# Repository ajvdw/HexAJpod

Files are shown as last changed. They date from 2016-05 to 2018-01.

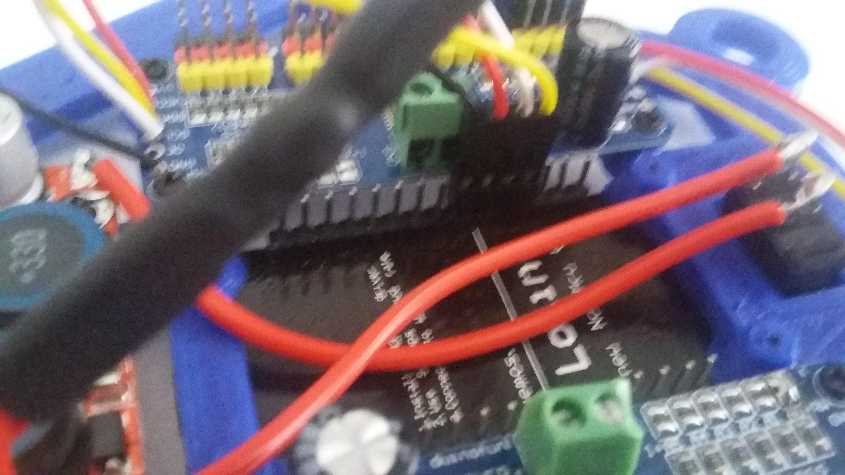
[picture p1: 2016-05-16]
media/nodemcu.jpg

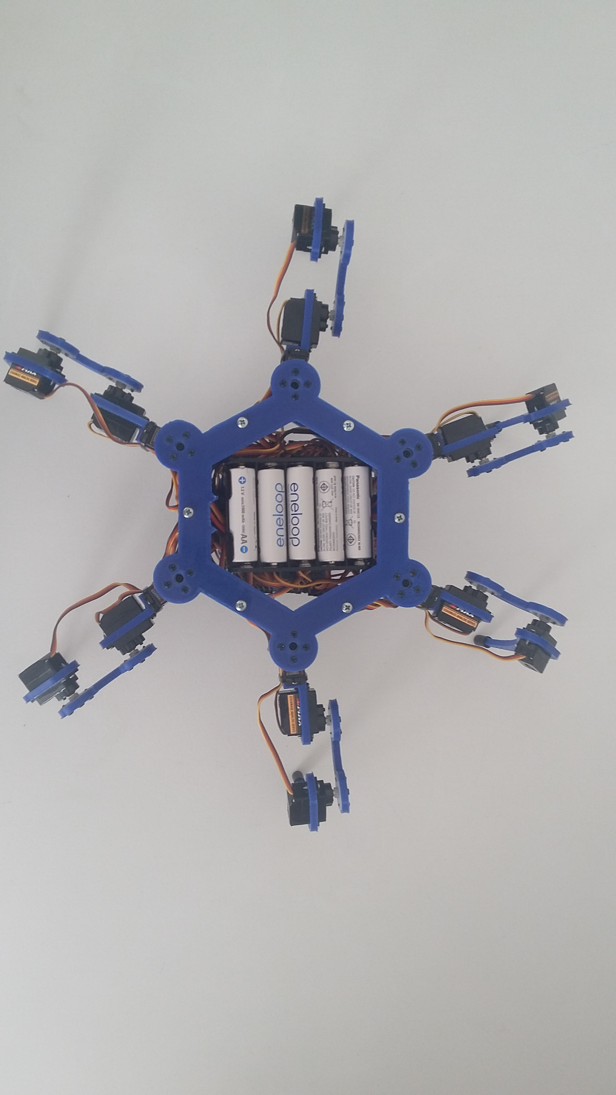
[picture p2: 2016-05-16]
media/top.jpg

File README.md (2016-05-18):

# HexAJpod
Hexapod ESP8266

This repository contains

- OpenScad cad design file for a 3d printed hexapod
- stl files for printing
- hexapod firmware for the ESP8266 Arduino IDE

Have a look at: https://youtu.be/j8itndjbUWE

The hexapod will act as an Wifi Access point.
You can connect to it using the password (bestkeptsecret).
Open a web page and visit http://192.168.4.1 
This opens a page with the remote control.
When fully loaded, a websocket connection is opened.

You should be able to build it for less than 100$

Bill of Materials:

1 NodeMCU - an ESP8266 development board by LoLin (v3)

2 Led / Servo drivers based on PCA9685

18 Servos by EMAX - ES08MA II, these have metal gears

5 NiMh AA Eneloop Batteries by Panasonic 

1 Battery holder for 5 AA batteries

1 DC-DC converter to converter to get a clean 3.3V

18 M3 screws 12mm

6 End caps (5mm)

6 Bearings 623Z (id=3mm, od=10mm)

6 M3 washers

6 M3 nuts

6 Brass 40mm Standoffs (M3 threaded)

75 2mm x 6mm screws

25 2mm x 8mm screws

I ordered the parts on eBay (http://r.ebay.com/3nL8qE)

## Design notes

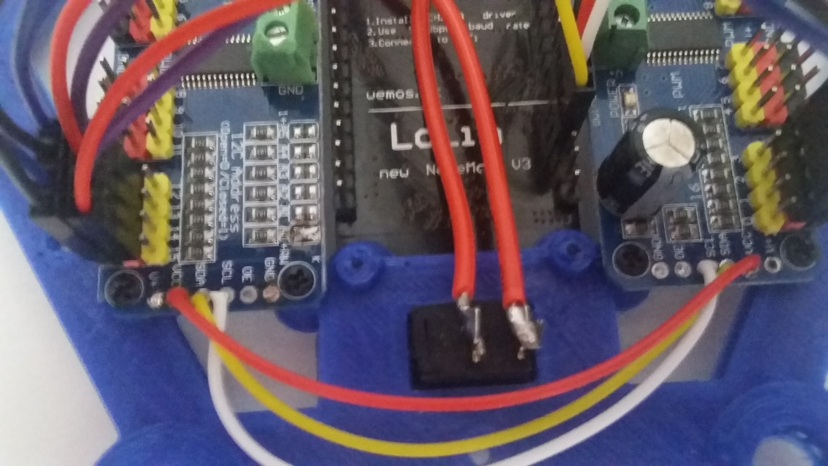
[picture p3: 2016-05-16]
media/switch.jpg

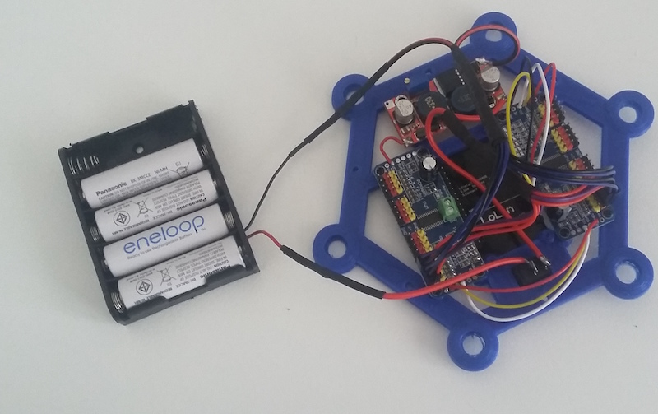
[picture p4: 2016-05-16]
media/thumbnail.jpg

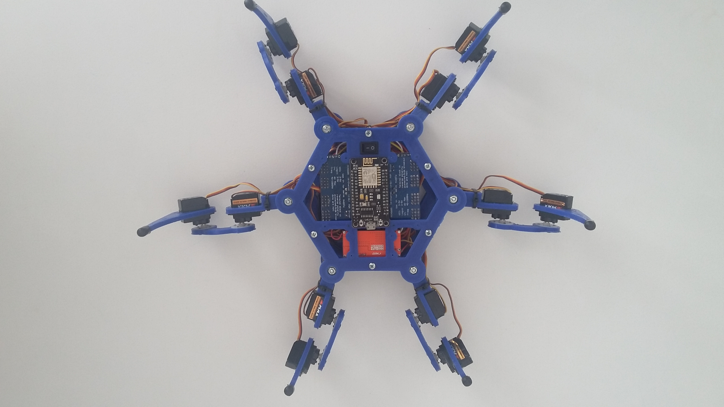
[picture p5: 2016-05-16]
media/bottom.jpg

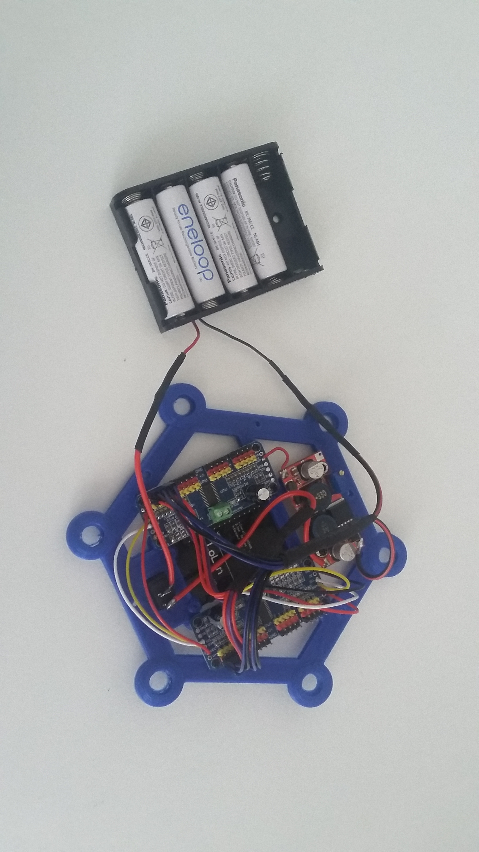
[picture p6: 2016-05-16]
media/internal.jpg

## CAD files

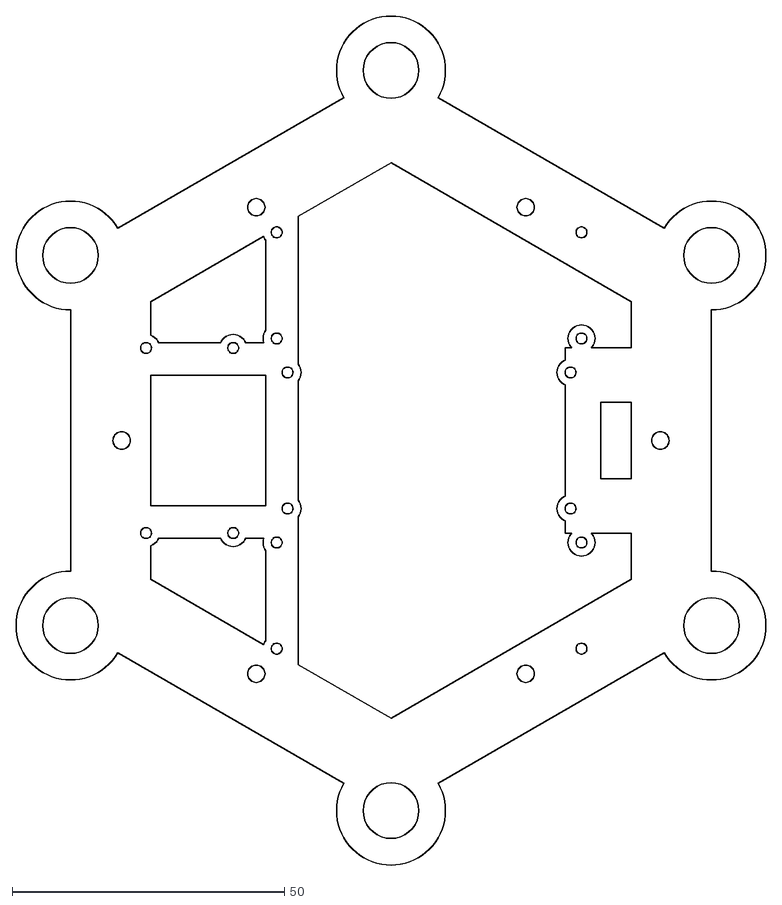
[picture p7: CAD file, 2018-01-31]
openscad/hexajpodbottom.dxf
137.8 x 156.0

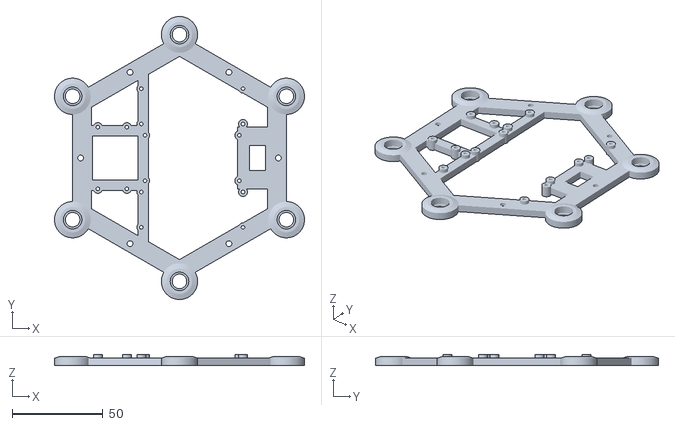
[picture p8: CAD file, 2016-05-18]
stl/bottom.stl
137.8 x 156.0 x 6.00

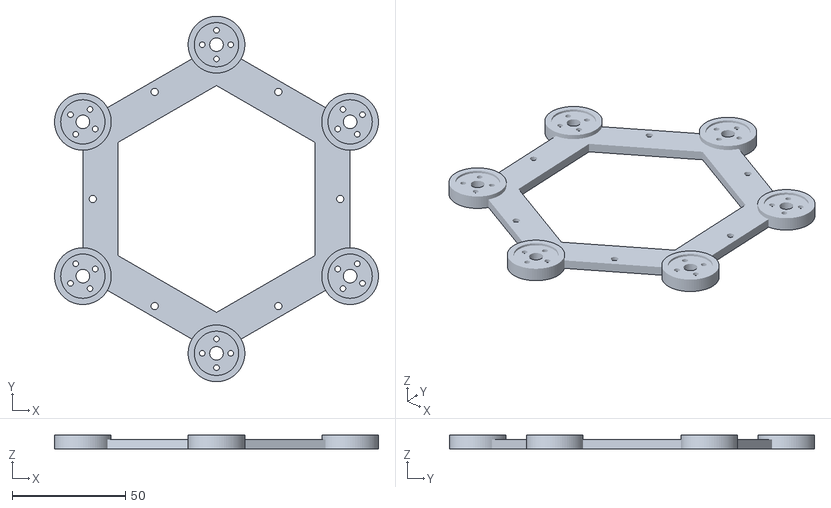
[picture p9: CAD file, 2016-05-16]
stl/top.stl
142.8 x 161.0 x 6.00

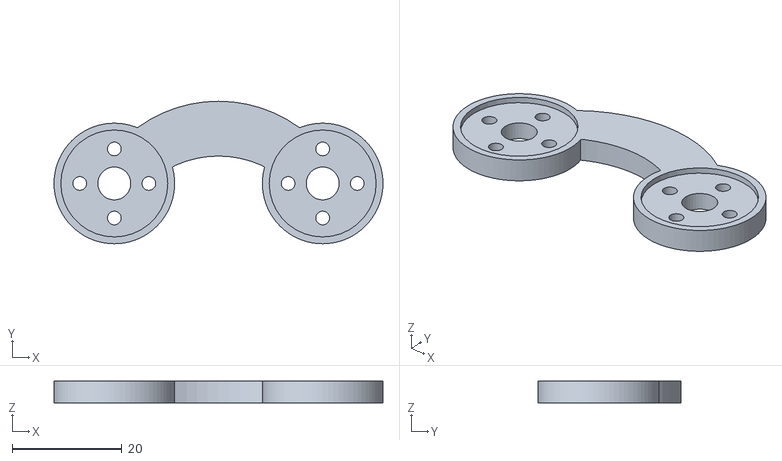
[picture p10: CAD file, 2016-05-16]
stl/femur.stl
60.0 x 26.0 x 4.00

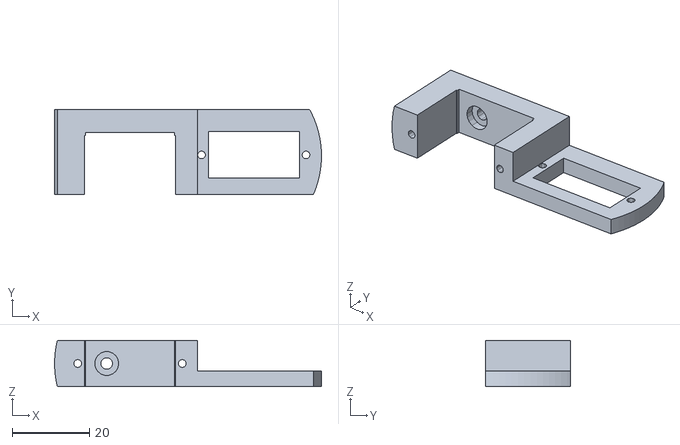
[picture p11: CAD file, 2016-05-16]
stl/coxa_l.stl
69.0 x 22.0 x 12.0

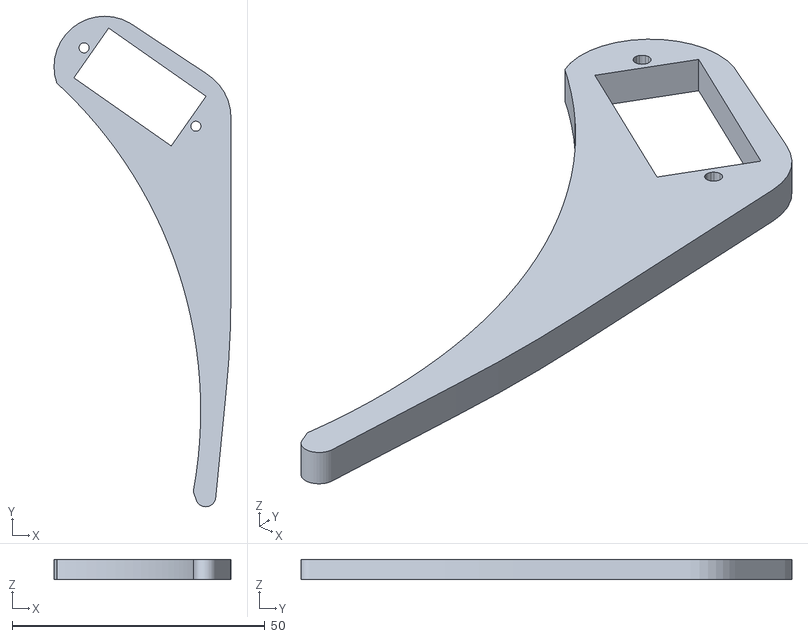
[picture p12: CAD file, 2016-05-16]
stl/tibia_r.stl
35.0 x 97.0 x 4.00

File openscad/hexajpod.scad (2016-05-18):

/* Hexapod by A.J. van de Werken */
/* May 2016                      */

servo_dist = 27.6;
servo_width = 11.5+0.5;
servo_length = 23+0.5;
servo_height = 15+0.5;

driverboard_width = 19.5;
driverboard_length = 56;
nodemcuboard_width = 25;
nodemcuboard_length  = 52;
dcdcboard_length = 16;
dcdcboard_width = 34;

tibia_thickness = 4;
femur_thickness = 4;

$fn=36;

module dcdcconverter(holes=false)
{
   if( !holes )
   {
        union()
        {
            translate([-dcdcboard_length/2,dcdcboard_width/2,0]) cylinder( d=5, h=6 );
            translate([-dcdcboard_length/2,-dcdcboard_width/2,0]) cylinder( d=5, h=6 );
            translate([dcdcboard_length/2,-dcdcboard_width/2,0]) cylinder( d=5, h=6 );
            translate([dcdcboard_length/2,dcdcboard_width/2,0]) cylinder( d=5, h=6 );
        }
    }
    else
    {
        union()
        {
            translate([-dcdcboard_length/2,dcdcboard_width/2,0]) cylinder( d=2, h=6 );
            translate([-dcdcboard_length/2,-dcdcboard_width/2,0]) cylinder( d=2, h=6 );
            translate([dcdcboard_length/2,-dcdcboard_width/2,0]) cylinder( d=2, h=6 );
            translate([dcdcboard_length/2,dcdcboard_width/2,0]) cylinder( d=2, h=6 );
        }
    }
}

module nodemcu(holes=false)
{
    if( !holes )
    {
        union()
        {
            translate([-nodemcuboard_length/2,nodemcuboard_width/2,0]) cylinder( d=5, h=6 );
            translate([-nodemcuboard_length/2,-nodemcuboard_width/2,0]) cylinder( d=5, h=6 );
            translate([nodemcuboard_length/2,-nodemcuboard_width/2,0]) cylinder( d=5, h=6 );
            translate([nodemcuboard_length/2,nodemcuboard_width/2,0]) cylinder( d=5, h=6 );
        }
    }
    else
    {
        union()
        {
            translate([-nodemcuboard_length/2,nodemcuboard_width/2,0]) cylinder( d=2, h=6 );
            translate([-nodemcuboard_length/2,-nodemcuboard_width/2,0]) cylinder( d=2, h=6 );
            translate([nodemcuboard_length/2,-nodemcuboard_width/2,0]) cylinder( d=2, h=6 );
            translate([nodemcuboard_length/2,nodemcuboard_width/2,0]) cylinder( d=2, h=6 );

        }
    }
}

module driver(holes=false)
{
    if(!holes)
    {
        union()
        {
            translate([-driverboard_length/2,driverboard_width/2,0]) cylinder( d=5, h=6 );
            translate([-driverboard_length/2,-driverboard_width/2,0]) cylinder( d=5, h=6 );
            translate([driverboard_length/2,-driverboard_width/2,0]) cylinder( d=5, h=6 );
            translate([driverboard_length/2,driverboard_width/2,0]) cylinder( d=5, h=6 );
        }
    }
    else
    {
        union()
        {
            translate([-driverboard_length/2,driverboard_width/2,0]) cylinder( d=2, h=6 );
            translate([-driverboard_length/2,-driverboard_width/2,0]) cylinder( d=2, h=6 );
            translate([driverboard_length/2,-driverboard_width/2,0]) cylinder( d=2, h=6 );
            translate([driverboard_length/2,driverboard_width/2,0]) cylinder( d=2, h=6 );
        }
    }
}

module servo()
{
    translate( [-servo_length/2, -servo_width/2, -servo_height/2 ] )
    cube( [servo_length, servo_width, servo_height ] );
    translate( [-servo_dist/2+0.3, 0, -1.5*servo_height ] )
    cylinder( d=2, h=servo_height*2, $fn=18 );
    translate( [servo_dist/2-0.3, 0, -1.5*servo_height ] )
    cylinder( d=2, h=servo_height*2, $fn=18 );
}


module tibia()
{
    difference()
    {
       hull()
        {
            cylinder( r=2, h=tibia_thickness);
            intersection()
            {
                translate( [-20,0,0]) cube([20,100,tibia_thickness] );
                translate( [190,40,0]) cylinder( r=195, h = tibia_thickness, $fn=180 );
            }
            translate( [5,75,0]) cylinder( r=10, h =tibia_thickness);
            translate( [20,85,0]) cylinder( r=10, h =tibia_thickness);
        }
        // Holes
        translate( [89,17,-1]) cylinder( r=88, h = tibia_thickness+2, $fn=180 );
        translate( [13,81,]) rotate([0,0,35]) servo();
    }
}



module femur()
{
    difference()
    {
        union()
        {
            translate( [-19,0,0] ) cylinder( d=22, h=femur_thickness, $fn=72 );
            translate( [ 19,0,0] ) cylinder( d=22, h=femur_thickness, $fn=72 );
            intersection()
            {
                difference()
                {
                    translate( [ 0,-10,0] ) cylinder( r=25, h=femur_thickness, $fn=60 );
                    translate( [ 0,-14,0] ) cylinder( r=19, h=femur_thickness, $fn=60 );
                }
                translate( [-60,0,0] ) cube( [120,60,femur_thickness]);
            }
        }

        for( t=[-19,19] )
        translate( [t,0,0] )
        { 
            translate([0,0,3]) cylinder( d=19.5, h=femur_thickness );
            cylinder( d=6, h=femur_thickness );
            for( a=[0:90:359] ) rotate([0,0,a]) translate([6.3,0,0]) cylinder( d=2.5, h=femur_thickness );
        }
        
    }
}

module coxa()
{
    rotate([90,0,0]) translate([-35,-2.75,0]) 
    intersection()
    {
        difference()
        {
            union()
            {
                translate([23,8.75,0]) cylinder( r=25,h=26, $fn=72 );
                translate([42,17.5,12]) rotate([90,0,0])cylinder( r=25,h=17.5, $fn=96 );
            }

            
            cube( [71,0,35] );
            translate( [6,0,6] ) cube( [23,17.5,35] );
            translate( [17.5,8.75,27.5-13]) servo();

            translate( [11.5,8.75,0] ) cylinder( d=3,h=10, $fn=18 );
            translate( [11.5,8.75,4] ) cylinder( d=6.2,h=10, $fn=18 );
       
            translate([70,25,22.5])
            rotate( [-90,0,0] )    
            rotate( [0,180,0] )
            {
                translate( [20.5,10.75,16]) servo();
                translate( [0,0,26] ) cube( [35,17.5,10] );
            }    
            
            translate( [35, 6.75, -1] ) cube([40,9,26]);
            
        }
        translate([-10,2.75,0]) cube( [90,12,22] );
    } 
}

module bottom()
{
    r1 =68;
    r2= 56;
    
    difference()
    {
        union()
        {
            difference()
            {   // Base
                rotate([0,0,30]) cylinder( r=r1, $fn=6, h=4 );
                translate([0,0,-1]) rotate([0,0,30]) cylinder( r=r2, $fn=6, h=6 );
            }
            
            for( a=[30:60:359]) 
            {   // Hips
                rotate([0,0,a]) translate( [r1, 0, 0] ) cylinder( d=20, h=4, $fn=72 );
                rotate([0,0,a]) translate( [r1, 0, 4] ) cylinder( d1=20 ,d2=14 , h=1, $fn=72 );
            }
            difference()
            {   // switch
                translate([41,0,2]) cube([18,34,4],  center=true );
                translate([43,0,0]) cube([9,14,10], center=true );
            }    
           
            // Boards support
            difference()
            {
                translate([-38,0,2]) cube([30,36,4], center=true );
                translate([-35,0,2]) cube([26,24,5], center=true );
            }
            translate([-20,0,2]) cube([6,100,4], center=true );
            

            translate([7,-28.5,0]) driver();
            translate([7,28.5,0]) driver();
            translate([7,0,0]) nodemcu();
            translate([-37,0,0]) dcdcconverter();
        }

        // Bearing holes
        for( a=[30:60:359]) 
        {
            rotate([0,0,a]) translate( [r1, 0, 1] ) cylinder( d=10.25, h=5, $fn=36 );
            rotate([0,0,a]) translate( [r1, 0, -1] ) cylinder( d=8, h=6, $fn=36 );
        }
        
        // Standoffs
        for( a=[0:60:359]) 
        {
            rotate([0,0,a]) translate( [r2-1.5, 0, 0] ) cylinder( d=3.2, h=5 );
        }

        // Holes
        translate([7,-28.5,0]) driver(true);
        translate([7,28.5,0]) driver(true);
        translate([7,0,0]) nodemcu(true);
        translate([-37,0,0]) dcdcconverter(true);

    }
   

        
}

module top()
{
    r1 =68;
    r2= 56;
    r3= 50;
    
    difference()
    {
        rotate([0,0,30]) union()
        {


            difference()
            {   // Base
                cylinder( r=r1, $fn=6, h=4 );
                translate([0,0,-1]) cylinder( r=r3, $fn=6, h=6 );
             }
            
            for( a=[0:60:359]) 
            {   // Hip joints
                rotate([0,0,a]) translate( [r1, 0, 0] ) cylinder( d=20, h=4, $fn=72 );
                rotate([0,0,a]) translate( [r1, 0, 0] ) cylinder( d=25, h=6, $fn=72 );
            }           
            
        }

        // Bearing holes
        for( a=[30:60:359]) 
        {
            rotate([0,0,a]) translate( [r1, 0, 5] ) cylinder( d=19.55, h=5, $fn=36 );
            rotate([0,0,a]) translate( [r1, 0, 0] ) cylinder( d=6, h=10, $fn=36 );
            rotate([0,0,a]) translate( [r1, 0, 0] )for( a=[0:90:359] ) rotate([0,0,a]) translate([6.3,0,0]) cylinder( d=2.5, h=10 );
        }
        // Standoffs
        for( a=[0:60:359]) 
        {
            rotate([0,0,a]) translate( [r2-1.5, 0, 0] ) cylinder( d=3.2, h=5 );
        }

    }
}
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

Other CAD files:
stl/coxa_r.stl
stl/tibia_l.stl
openscad/hexajpod_t.scad

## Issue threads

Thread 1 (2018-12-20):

trying to run this on core 2.4

Rtully, 2018-12-20:
Hi i'm trying to run this first on latest core with no luck and then with core 2.4-rc1 and 2.3 it compiles OK, the web control app opens ok but no movement on servos, have tried pins D1 D2 and pins D5 D6 and other combinations with no luck, any ideas please?

ajvdw, 2018-12-20:
Please note that it runs on an ESP8266. The ESP uses I2c to control 2 12-bit PWM/Servo Driver-I2C interface Module each controlling 16 channels

Rtully, 2018-12-20:
Yes I know, that is what i have setup. the i2c doesn't seem to be communicating with the PCA9685 s, I can see the servo messages in the serial monitor when i connect to the webapp but the message doesn't seem to be reaching the servo drivers.

ajvdw, 2018-12-20:
Does your i2c communication work? Proper addresses?

Rtully, 2018-12-21:
If i run a test sketch with the current adafruit driver on ESP core 2.4.2 the i2c works ok, (but thats with a "wire.begin (4, 5)"). Then your code won't compile on 2.4.2 so I got it to compile using 2.3 core, the webapp etc works fine but no movement on servos at all (i think its the i2c) I have tried using several pins but the defaults should be GPIO4 and GPIO5 by default no? Lastly I have tried to port the code to work with the current Adafruit PWM driver by changing the call in phoenix.cpp to "// Define our ServoDriver objects
Adafruit_PWMServoDriver g_ServoDriverR = Adafruit_PWMServoDriver(0x41);     // our global servo driver right side legs
Adafruit_PWMServoDriver g_ServoDriverL = Adafruit_PWMServoDriver(0x40);"
I changed the "include library" to the Adafruit_PWMServoDriver.h instead of include "servodriver.h"
I also had to change the server line in Hexapod8266.ino "// Web Server
ESP8266WebServer server (80);" It all connects the same as the original code on 2.3. The webapp connects fine on my phone and as soon as it connects in the serial monitor on the IDE I can see the loop of servo commands running. This is what leads me to think it's an i2c pin problem? I'm using a nodeMCU V1.0 12E and two PCAS9683's. Thanks so much for any help, I've been two days trying to get this running.

Rtully, 2018-12-21:
what i'm getting on serial monitor with debug core.
Setting PWM 0: 0->369
Setting PWM 1: 0->210
Setting PWM 2: 0->259
Setting PWM 15: 0->375
Setting PWM 14: 0->540
Setting PWM 13: 0->491
Setting PWM 4: 0->375
Setting PWM 5: 0->210
Setting PWM 6: 0->259
Setting PWM 11: 0->375
Setting PWM 10: 0->540
Setting PWM 9: 0->491
Setting PWM 8: 0->368
Setting PWM 9: 0->208
Setting PWM 10: 0->255
Setting PWM 7: 0->375
etc etc...

ajvdw, 2018-12-21:
I agree, it must be the i2c code.
You should first try some sample  (for the Adafruit driver) code to get 1 servo to move.
Than work out the differences with my code. It comes down to 3 or 4 lines of code.

https://learn.adafruit.com/16-channel-pwm-servo-driver/hooking-it-up
I remember adjusting the Adafruit driver code because the original didn't work in my case.

Rtully, 2018-12-21:
i have gone through the adafruit code and it all seems pretty similar, apart from the lines that didnt work originally for you which have changed a bit since. i have also tried with your servo driver code, i have the pwm drivers attached to GPIO 4 and 5 and with a i2c checker sketch they show up fine and with correct addresses. I have also had servos moving fine using adafruit test sketches with adafruit drivers....

Rtully, 2018-12-21:
handleFileRead: /remote.css
handleFileRead: /ocanvas-2.8.3.min.js
[0] Connected from 192.168.4.2 url: /
Setting PWM 0: 0->375
Setting PWM 1: 0->210
Setting PWM 2: 0->259
Setting PWM 15: 0->375
Setting PWM 14: 0->540
Setting PWM 13: 0->491
Setting PWM 4: 0->375
Setting PWM 5: 0->210
Setting PWM 6: 0->259
Setting PWM 11: 0->375
Setting PWM 10: 0->540
Setting PWM 9: 0->491
Setting PWM 8: 0->375

Rtully, 2018-12-21:
the previous is the original code runing on core 2.3. This is the modified code (adafruit driver) runing on lates 2.5.0 beta2:

Hexapod v0.2
Setup SPIFFS

Setup Wifi
Init Controller
Config loaded
Start Websocket
Start mDNS
Start Webserver
Setup i2c
Init Phoenix
Attempting to set freq 1000.00
Estimated pre-scale: 5.78
Final pre-scale: 6
Mode now 0xFF
Attempting to set freq 60.00
Estimated pre-scale: 112.03
Final pre-scale: 112
Mode now 0xFF
Attempting to set freq 1000.00
Estimated pre-scale: 5.78
Final pre-scale: 6
Mode now 0xFF
Attempting to set freq 60.00
Estimated pre-scale: 112.03
Final pre-scale: 112
Mode now 0xFF
Setting PWM 0: 0->375
Setting PWM 1: 0->375
Setting PWM 2: 0->375
Setting PWM 15: 0->375
Setting PWM 14: 0->375
Setting PWM 13: 0->375
Setting PWM 4: 0->375
Setting PWM 5: 0->375
Setting PWM 6: 0->375
Setting PWM 11: 0->375
Setting PWM 10: 0->375
Setting PWM 9: 0->375
Setting PWM 8: 0->375
Setting PWM 9: 0->375
Setting PWM 10: 0->375
Setting PWM 7: 0->375
Setting PWM 6: 0->375
Setting PWM 5: 0->375
Running loop ...

Rtully, 2018-12-21:
ok sorry 2.5 beta2 didnt work. in 2.4.2 it is connecting and recieveing from the webapp but still no joy with the servos themselves:

:rch 46, 13
[WS][0][handleWebsocketWaitFor] size: 2 cWsRXsize: 0
[readCb] n: zu t: 2
:rch 59, 10
:rd 2, 59, 0
:rdi 12, 2
[WS][0][handleWebsocketWaitFor][readCb] size: 2 ok: 1
[WS][0][handleWebsocket] ------- read massage frame -------
[WS][0][handleWebsocket] fin: 1 rsv1: 0 rsv2: 0 rsv3 0  opCode: 1
[WS][0][handleWebsocket] mask: 1 payloadLen: 6
[WS][0][handleWebsocketWaitFor] size: 6 cWsRXsize: 2
[readCb] n: zu t: 4
:rd 4, 69, 2
:rdi 10, 4
[WS][0][handleWebsocketWaitFor][readCb] size: 6 ok: 1
[WS][0][handleWebsocket] ------- read massage frame -------
[WS][0][handleWebsocket] fin: 1 rsv1: 0 rsv2: 0 rsv3 0  opCode: 1
[WS][0][handleWebsocket] mask: 1 payloadLen: 6
[readCb] n: zu t: 6
:rd 6, 69, 6
:rdi 6, 6
:c 6, 12, 69
[WS][0][handleWebsocket] text: #x,-50
:rch 57, 12
:rch 69, 12
[WS][0][handleWebsocketWaitFor] size: 2 cWsRXsize: 0
[readCb] n: zu t: 2
:rd 2, 81, 0
:rdi 11, 2
[WS][0][handleWebsocketWaitFor][readCb] size: 2 ok: 1
[WS][0][handleWebsocket] ------- read massage frame -------
[WS][0][handleWebsocket] fin: 1 rsv1: 0 rsv2: 0 rsv3 0  opCode: 1
[WS][0][handleWebsocket] mask: 1 payloadLen: 5
[WS][0][handleWebsocketWaitFor] size: 6 cWsRXsize: 2
[readCb] n: zu t: 4
:rd 4, 81, 2
:rdi 9, 4
[WS][0][handleWebsocketWaitFor][readCb] size: 6 ok: 1
[WS][0][handleWebsocket] ------- read massage frame -------
[WS][0][handleWebsocket] fin: 1 rsv1: 0 rsv2: 0 rsv3 0  opCode: 1
[WS][0][handleWebsocket] mask: 1 payloadLen: 5
[readCb] n: zu t: 5
:rd 5, 81, 6
:rdi 5, 5
:c 5, 11, 81
[WS][0][handleWebsocket] text: #y,69
:rch 70, 12
:rch 82, 12
[WS][0][handleWebsocketWaitFor] size: 2 cWsRXsize: 0
[readCb] n: zu t: 2
:rd 2, 94, 0
:rdi 12, 2
[WS][0][handleWebsocketWaitFor][readCb] size: 2 ok: 1
[WS][0][handleWebsocket] ------- read massage frame -------
[WS][0][handleWebsocket] fin: 1 rsv1: 0 rsv2: 0 rsv3 0  opCode: 1
[WS][0][handleWebsocket] mask: 1 payloadLen: 6
[WS][0][handleWebsocketWaitFor] size: 6 cWsRXsize: 2
[readCb] n: zu t: 4
:rd 4, 94, 2
:rdi 10, 4
[WS][0][handleWebsocketWaitFor][readCb] size: 6 ok: 1
[WS][0][handleWebsocket] ------- read massage frame -------
[WS][0][handleWebsocket] fin: 1 rsv1: 0 rsv2: 0 rsv3 0  opCode: 1
[WS][0][handleWebsocket] mask: 1 payloadLen: 6
[readCb] n: zu t: 6
:rd 6, 94, 6
:rdi 6, 6
:c 6, 12, 94
[WS][0][handleWebsocket] text: #x,-94
:rch 82, 11
:rch 93, 12
Setting PWM 0: 0->377
Setting PWM 1: 0->228
Setting PWM 2: 0->286
Setting PWM 15: 0->375
Setting PWM 14: 0->600
Setting PWM 13: 0->600
Setting PWM 4: 0->339
Setting PWM 5: 0->150
Setting PWM 6: 0->150
Setting PWM 11: 0->359
Setting PWM 10: 0->549
Setting PWM 9: 0->504
Setting PWM 8: 0->389
Setting PWM 9: 0->195
Setting PWM 10: 0->239
Setting PWM 7: 0->388
Setting PWM 6: 0->522
Setting PWM 5: 0->464

Rtully, 2018-12-21:
this is the serial on boot in 2.4.2:
SDK:2.2.1(cfd48f3)/Core:2.4.2/lwIP:2.0.3(STABLE-2_0_3_RELEASE/glue:arduino-2.4.1-13-g163bb82)/BearSSL:6d1cefc

Hexapod v0.2
Setup SPIFFS
SPIFFSImpl: allocating 512+240+1400=2152 bytes
SPIFFSImpl: mounting fs @300000, size=fb000, block=2000, page=100
SPIFFSImpl: mount rc=0
FS File: /favicon.ico, size: 1.12KB
FS File: /apple-touch-icon-120x120.png, size: 1.82KB
FS File: /remote.css, size: 609B
FS File: /ocanvas-2.8.3.min.js, size: 71.68KB
FS File: /rotateplease.png, size: 1.75KB

Setup Wifi
Init Controller
Config loaded
Start Websocket
[WS-Server] Server Started.
Start mDNS
Start Webserver
Setup i2c
Init Phoenix
Attempting to set freq 1000.00
Estimated pre-scale: 5.78
Final pre-scale: 6
Mode now 0xFF
Attempting to set freq 60.00
Estimated pre-scale: 112.03
Final pre-scale: 112
Mode now 0xFF
Attempting to set freq 1000.00
Estimated pre-scale: 5.78
Final pre-scale: 6
Mode now 0xFF
Attempting to set freq 60.00
Estimated pre-scale: 112.03
Final pre-scale: 112
Mode now 0xFF
Setting PWM 0: 0->375
Setting PWM 1: 0->375
Setting PWM 2: 0->375
Setting PWM 15: 0->375
Setting PWM 14: 0->375
Setting PWM 13: 0->375

ajvdw, 2018-12-21:
The changes I made are in this function, it's more efficient if you look at the number of commands send over the i2c lines.
You can revert back to the code you used when the servo was moving .....

void Servodriver::setPWM(uint8_t num, uint16_t on, uint16_t off) {
  //Serial.print("Setting PWM "); Serial.print(num); Serial.print(": "); Serial.print(on); Serial.print("->"); Serial.println(off);

  //This code didn't seem to work with chained i2c servo boards
  //Wire.beginTransmission(_i2caddr);
  //Wire.write(LED0_ON_L+4*num);
  //Wire.write(on);
  //Wire.write(on>>8);
  //Wire.write(off);
  //Wire.write(off>>8);
  //Wire.endTransmission();

  write8((byte)(LED0_ON_L + 4 * num), (byte)on);
  write8((byte)(LED0_ON_H + 4 * num), (byte)(on >> 8));
  write8((byte)(LED0_OFF_L + 4 * num), (byte)off);
  write8((byte)(LED0_OFF_H + 4 * num), (byte)(off >> 8));
}

Rtully, 2018-12-22:
Ok, I finally got it working with ESP core 2.4.2. The adafruit driver just doesn't work, i can get some servo noises when it connects but it has issues with the phoenix code as you said. I modified slightly your servo code to update some things that have changed in ESP Core 2.4.2 and Arduino since you wrote the original file:

the server line in Hexapod8266.h to:
// Web Server
ESP8266WebServer server (80);

and in the Servodriver.h changing:
"val = min(val, (4095);"
to
"val = min(val, (uint16_t)4095);"
I think that is all that changed in the end....
Onwards and upwards! Thanks so much for the help, now I plan to try to create a "controller" with a second esp8266 as slave and a gyro board.... Hopefully i can just send the same codes as the webapp javascript.

Rtully, 2018-12-22:
Sorry cold you tell me where on each PCA board goes each leg? Thanks

ajvdw, 2018-12-24:
Board 1
0 RightRear Coxa
1 RightRear Femur
2 RightRear Tibia
4 RightMiddle Coxa
5 RightMiddle Femur
6 RightMiddle Tibia
8 RightFront Coxa
9 RightFront Femur
10 RightFront Tibia

Board 2
0 LeftRear Coxa
1 LeftRear Femur
2 LeftRear Tibia
4 LeftMiddle Coxa
5 LeftMiddle Femur
6 LeftMiddle Tibia
8 LeftFront Coxa
9 LeftFront Femur
10 LeftFront Tibia

Have a look at the function StartUpdateServos()
In that function all servo's are set one by one.

Rtully, 2018-12-25:
thanks for all the help. Happy Christmas.

Closed 2018-12-20.

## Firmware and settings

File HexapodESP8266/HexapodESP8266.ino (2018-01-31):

//=============================================================================
//Project HexAJpod - AJvdW
//Date    15 Apr 2016 - v0.2
//=============================================================================
#include <Arduino.h>
#include <Wire.h>
#include <ESP8266WiFi.h>
#include <ESP8266WiFiGeneric.h>
#include <WebSocketsServer.h>
#include <ESP8266WebServer.h>
#include <ESP8266mDNS.h>
#include <EEPROM.h>
#include <FS.h>

#include "index.html.h"
#include "calibrate.html.h"
#include "WebController.h"
#include "Phoenix.h"

const char WiFiAPPSK[] = "bestkeptsecret";

// Web Server
ESP8266WebServer server = ESP8266WebServer(80);
// Web Socket server
WebSocketsServer webSocket = WebSocketsServer(81);
// Web Controller 
WebController g_WebController; 
// Phoenix Robot Control Class
Phoenix g_Phoenix;

void webSocketEvent(uint8_t num, WStype_t type, uint8_t * payload, size_t length) 
{   // handler websocket data
    static int hx,hy,hz;
    
    switch(type) {
        case WStype_DISCONNECTED:
            g_WebController.SwitchOff();
            Serial.printf("[%u] Disconnected!\n", num);
            break;
        case WStype_CONNECTED: 
          {
            IPAddress ip = webSocket.remoteIP(num);
            Serial.printf("[%u] Connected from %d.%d.%d.%d url: %s\n", num, ip[0], ip[1], ip[2], ip[3], payload);

            // send message to client
            webSocket.sendTXT(num, "Hexapod connected");
            g_WebController.SwitchOn();

          }
            break;
        case WStype_TEXT:      //bool btnBlue, bool btnRed, bool btnYellow, bool bntGreen, int joyX, int joyY, int joyZ  
            //Serial.printf("[%u] get Text: %s\n", num, payload);
            if(payload[0] == '#') 
            {
                // we get data
                if( payload[1] == 'R')
                {
                  g_WebController.ButtonRed();
                  webSocket.sendTXT(num,g_WebController.Status().c_str());
                }
                if( payload[1] == 'G')
                {
                  g_WebController.ButtonGreen();
                  webSocket.sendTXT(num,g_WebController.Status().c_str());
                }
                if( payload[1] == 'B')
                {
                  g_WebController.ButtonBlue();
                  webSocket.sendTXT(num,g_WebController.Status().c_str());
                }
                if( payload[1] == 'Y')
                {
                  g_WebController.ButtonYellow();
                  webSocket.sendTXT(num,g_WebController.Status().c_str());
                }
                if( payload[1] == 'x')
                {
                    hx = min(128,max(-127,atoi( (char *)(&(payload[3] )))));
                    g_WebController.JoystickMove( hx,hy,hz );
                }                  
                if( payload[1] == 'y')
                {
                    hy = min(128,max(-127,atoi( (char *)(&(payload[3] )))));
                    g_WebController.JoystickMove( hx,hy,hz );
                }                  
                if( payload[1] == 'z')
                {
                    hz = min(128,max(-127,atoi( (char *)(&(payload[3] )))));
                    g_WebController.JoystickMove( hx,hy,hz );
                }                  
            }
            break;
    }

}

void setupWiFi()
{ // setup Wifi
//  ESP.eraseConfig();
//  WiFi.setAutoConnect(false);
//  WiFi.disconnect(true);
  
  WiFi.mode(WIFI_AP);

  uint8_t mac[6];
  char apStr[18] = {0};
  WiFi.macAddress(mac);
  //sprintf(apStr, "Hexapod %s", "test" );
  sprintf(apStr, "Hexapod %02X%02X%02X%02X",  mac[2], mac[3], mac[4], mac[5]);

  WiFi.softAP(apStr, WiFiAPPSK, 9);
}

void updateGait()
{ // Helper function
  g_Phoenix.GaitSelect();
}

String getContentType(String filename)
{ // determine content type
  if(server.hasArg("download")) return "application/octet-stream";
  else if(filename.endsWith(".htm")) return "text/html";
  else if(filename.endsWith(".html")) return "text/html";
  else if(filename.endsWith(".css")) return "text/css";
  else if(filename.endsWith(".js")) return "application/javascript";
  else if(filename.endsWith(".png")) return "image/png";
  else if(filename.endsWith(".gif")) return "image/gif";
  else if(filename.endsWith(".jpg")) return "image/jpeg";
  else if(filename.endsWith(".ico")) return "image/x-icon";
  else if(filename.endsWith(".xml")) return "text/xml";
  else if(filename.endsWith(".pdf")) return "application/x-pdf";
  else if(filename.endsWith(".zip")) return "application/x-zip";
  else if(filename.endsWith(".gz")) return "application/x-gzip";
  return "text/plain";
}

bool handleFileRead(String path)
{ // read data from SPIFF
  Serial.println("handleFileRead: " + path);
  if(path.endsWith("/")) path += "index.htm";
  String contentType = getContentType(path);
  String pathWithGz = path + ".gz";
  if(SPIFFS.exists(pathWithGz) || SPIFFS.exists(path)){
    if(SPIFFS.exists(pathWithGz))
      path += ".gz";
    File file = SPIFFS.open(path, "r");
    size_t sent = server.streamFile(file, contentType);
    file.close();
    return true;
  }
  return false;
}

String formatBytes(size_t bytes)
{ // pretty size
  if (bytes < 1024) return String(bytes)+"B";
  else if(bytes < (1024 * 1024)) return String(bytes/1024.0)+"KB";
  else if(bytes < (1024 * 1024 * 1024)) return String(bytes/1024.0/1024.0)+"MB";
  return String(bytes/1024.0/1024.0/1024.0)+"GB";
}

void EEPROMWritelong(int address, long value)
{ // Write the 4 bytes into the eeprom memory.
  EEPROM.write(address + 0, (byte)(value >> 0) & 0xFF);
  EEPROM.write(address + 1, (byte)(value >> 8) & 0xFF);
  EEPROM.write(address + 2, (byte)(value >> 16) & 0xFF);
  EEPROM.write(address + 3, (byte)(value >> 24) & 0xFF);
}

long EEPROMReadlong(long address)
{ // Return the recomposed long by using bitshift.
  return (((long)EEPROM.read(address) << 0) & 0xFF) + 
         (((long)EEPROM.read(address+1) << 8) & 0xFFFF) + 
         (((long)EEPROM.read(address+2) << 16) & 0xFFFFFF) +
         (((long)EEPROM.read(address+3) << 24) & 0xFFFFFFFF);
}

void SaveConfig()
{ // Save calibration config to EEPROM
  for( int legnr=0; legnr< 6; legnr++ )
  {
    EEPROMWritelong(legnr*48, g_Phoenix.cCoxaMin1[legnr]);
    EEPROMWritelong(legnr*48+4, g_Phoenix.cFemurMin1[legnr]);
    EEPROMWritelong(legnr*48+8, g_Phoenix.cTibiaMin1[legnr]);
    EEPROMWritelong(legnr*48+12, g_Phoenix.cCoxaMax1[legnr]);
    EEPROMWritelong(legnr*48+16, g_Phoenix.cFemurMax1[legnr]);
    EEPROMWritelong(legnr*48+20, g_Phoenix.cTibiaMax1[legnr]);
    EEPROMWritelong(legnr*48+24, g_Phoenix.cCoxaPWMC[legnr]);
    EEPROMWritelong(legnr*48+28, g_Phoenix.cFemurPWMC[legnr]);
    EEPROMWritelong(legnr*48+32, g_Phoenix.cTibiaPWMC[legnr]);
    EEPROMWritelong(legnr*48+36, g_Phoenix.cCoxaPWMD[legnr]);
    EEPROMWritelong(legnr*48+40, g_Phoenix.cFemurPWMD[legnr]);
    EEPROMWritelong(legnr*48+44, g_Phoenix.cTibiaPWMD[legnr]);
  }
  
  EEPROM.write(288,'H');
  EEPROM.write(289,'E');
  EEPROM.write(290,'X');
  EEPROM.write(291,'C');
  EEPROM.commit();
}

boolean LoadConfig()
{ // Load calibration config from EEPROM
  if (EEPROM.read(288) == 'H' && EEPROM.read(289) == 'E' && EEPROM.read(290) == 'X'  && EEPROM.read(291) == 'C' )
  {
    for( int legnr=0; legnr< 6; legnr++ )
    {
      g_Phoenix.cCoxaMin1[legnr] = EEPROMReadlong(legnr*48);
      g_Phoenix.cFemurMin1[legnr] = EEPROMReadlong(legnr*48+4);
      g_Phoenix.cTibiaMin1[legnr] = EEPROMReadlong(legnr*48+8);
      g_Phoenix.cCoxaMax1[legnr] = EEPROMReadlong(legnr*48+12);
      g_Phoenix.cFemurMax1[legnr] = EEPROMReadlong(legnr*48+16);
      g_Phoenix.cTibiaMax1[legnr] = EEPROMReadlong(legnr*48+20);
      g_Phoenix.cCoxaPWMC[legnr] = EEPROMReadlong(legnr*48+24);
      g_Phoenix.cFemurPWMC[legnr] = EEPROMReadlong(legnr*48+28);
      g_Phoenix.cTibiaPWMC[legnr] = EEPROMReadlong(legnr*48+32);
      g_Phoenix.cCoxaPWMD[legnr] = EEPROMReadlong(legnr*48+36);
      g_Phoenix.cFemurPWMD[legnr] = EEPROMReadlong(legnr*48+40);
      g_Phoenix.cTibiaPWMD[legnr] = EEPROMReadlong(legnr*48+44);
    }  
    return true;
  }
  else
    return false;
}

void send_status_json()
{ // status json
  //Serial.println("status");
  server.send( 200, "application/json", g_Phoenix.StatusJSON() );  
}

void send_calibrate_html()
{ // calibration page
  String leg[] = {"RR","RC","RF","LR","LC","LF"};
  String v;
  short  c;
  
  String html = calib_html;
  
  if (server.args() > 0  ) 
  {
    String temp = "";
    for ( uint8_t i = 0; i < server.args(); i++ ) {
      int legnr =0;
      if( server.argName(i).substring(0,1) == "L" ) legnr += 3;
      if( server.argName(i).substring(1,2) == "C" ) legnr += 1;
      else if( server.argName(i).substring(1,2) == "F" ) legnr += 2;
      if( server.argName(i).substring(2) == "C_MINANG" ) g_Phoenix.cCoxaMin1[legnr] = server.arg(i).toInt();
      if( server.argName(i).substring(2) == "F_MINANG" ) g_Phoenix.cFemurMin1[legnr] = server.arg(i).toInt();
      if( server.argName(i).substring(2) == "T_MINANG" ) g_Phoenix.cTibiaMin1[legnr] = server.arg(i).toInt();
      if( server.argName(i).substring(2) == "C_MAXANG" ) g_Phoenix.cCoxaMax1[legnr] = server.arg(i).toInt();
      if( server.argName(i).substring(2) == "F_MAXANG" ) g_Phoenix.cFemurMax1[legnr] = server.arg(i).toInt();
      if( server.argName(i).substring(2) == "T_MAXANG" ) g_Phoenix.cTibiaMax1[legnr] = server.arg(i).toInt();
      if( server.argName(i).substring(2) == "C_PWMC" )   g_Phoenix.cCoxaPWMC[legnr] = server.arg(i).toInt();
      if( server.argName(i).substring(2) == "F_PWMC" )   g_Phoenix.cFemurPWMC[legnr] = server.arg(i).toInt();
      if( server.argName(i).substring(2) == "T_PWMC" )   g_Phoenix.cTibiaPWMC[legnr] = server.arg(i).toInt();
      if( server.argName(i).substring(2) == "C_PWMDEG" ) g_Phoenix.cCoxaPWMD[legnr] = server.arg(i).toInt();
      if( server.argName(i).substring(2) == "F_PWMDEG" ) g_Phoenix.cFemurPWMD[legnr] = server.arg(i).toInt();
      if( server.argName(i).substring(2) == "T_PWMDEG" ) g_Phoenix.cTibiaPWMD[legnr] = server.arg(i).toInt();
      if(  server.argName(i) == "move" )
      {
         // Save Settings 
         g_Phoenix.StartUpdateServos();
      }
      if(  server.argName(i) == "save" )
      {
         // Save Settings 
         SaveConfig();
      }
      if(  server.argName(i) == "load" )
      {
         // Load Settings 
         LoadConfig();
      }
    }
  }

  for( int LegIndex=0; LegIndex<6; LegIndex++ )
  {
    for( int t=0; t<15; t++ )
    {
      switch( t )
      {       
        case 0:  v = leg[LegIndex] + "C_ANG";    c = g_Phoenix.CoxaAngle1[LegIndex];  break;  
        case 1:  v = leg[LegIndex] + "F_ANG";    c = g_Phoenix.FemurAngle1[LegIndex]; break;  
        case 2:  v = leg[LegIndex] + "T_ANG";    c = g_Phoenix.TibiaAngle1[LegIndex]; break;  
        case 3:  v = leg[LegIndex] + "C_MINANG"; c = g_Phoenix.cCoxaMin1[LegIndex];   break;  
        case 4:  v = leg[LegIndex] + "F_MINANG"; c = g_Phoenix.cFemurMin1[LegIndex];  break;  
        case 5:  v = leg[LegIndex] + "T_MINANG"; c = g_Phoenix.cTibiaMin1[LegIndex];  break;  
        case 6:  v = leg[LegIndex] + "C_MAXANG"; c = g_Phoenix.cCoxaMax1[LegIndex];   break;  
        case 7:  v = leg[LegIndex] + "F_MAXANG"; c = g_Phoenix.cFemurMax1[LegIndex];  break;  
        case 8:  v = leg[LegIndex] + "T_MAXANG"; c = g_Phoenix.cTibiaMax1[LegIndex];  break;  
        case 9:  v = leg[LegIndex] + "C_PWMC";   c = g_Phoenix.cCoxaPWMC[LegIndex];   break;  
        case 10: v = leg[LegIndex] + "F_PWMC";   c = g_Phoenix.cFemurPWMC[LegIndex];  break;  
        case 11: v = leg[LegIndex] + "T_PWMC";   c = g_Phoenix.cTibiaPWMC[LegIndex];  break;  
        case 12: v = leg[LegIndex] + "C_PWMDEG"; c = g_Phoenix.cCoxaPWMD[LegIndex];   break;  
        case 13: v = leg[LegIndex] + "F_PWMDEG"; c = g_Phoenix.cFemurPWMD[LegIndex];  break;  
        case 14: v = leg[LegIndex] + "T_PWMDEG"; c = g_Phoenix.cTibiaPWMD[LegIndex];  break;     
      }
      html.replace( String("%") + v + String("%"), String(c) );
    }
  }
  server.send ( 200, "text/html", html);
}

void backgroundProcessing( int ms )
{ // don't stop the web
  int wait = millis()+ms/20; // We've got a timing issue
  server.handleClient();
  while( millis() < wait  ) // Need to catch cycle through
  {  
      webSocket.loop();
      yield();
  }
}

void setup() 
{   // main Setup
    Serial.begin(115200);
    Serial.printf("\n\n\nHexapod v0.2\n");
    
    Serial.printf("Setup SPIFFS\n");
    SPIFFS.begin();
    {
      Dir dir = SPIFFS.openDir("/");
      while (dir.next()) 
      {    
        String fileName = dir.fileName();
        size_t fileSize = dir.fileSize();
        Serial.printf("FS File: %s, size: %s\n", fileName.c_str(), formatBytes(fileSize).c_str());
      }
        Serial.printf("\n");
    }
    
    Serial.printf("Setup Wifi\n");
    setupWiFi();
       

    Serial.printf("Init Controller\n");
    g_WebController.Init();
   
    EEPROM.begin(512);
    if( LoadConfig() ) // Load Calibration Config
      Serial.printf("Config loaded\n");
    else
      Serial.printf("Config not found (calibrate!)\n");
    
    // start webSocket server
    Serial.printf("Start Websocket\n"); 
    webSocket.begin();
    webSocket.onEvent(webSocketEvent);

    if(MDNS.begin("esp8266")) 
        Serial.println("Start mDNS");

    server.on( "/", [](){ server.send ( 200, "text/html", index_html );} );
    server.on( "/calibrate", send_calibrate_html ); 
    server.on( "/status", send_status_json ); 
    
    //called when the url is not defined here
    //use it to load content from SPIFFS
    server.onNotFound([](){ if(!handleFileRead(server.uri())) server.send(404, "text/plain", "FileNotFound"); });

    Serial.printf("Start Webserver\n"); 
    server.begin();

    // Add service to MDNS
    MDNS.addService("http", "tcp", 80);
    MDNS.addService("ws", "tcp", 81);

    Serial.printf("Setup i2c\n");
    Wire.begin(D3, D4); //pins D3 and D4

    Serial.printf("Init Phoenix\n");
    g_Phoenix.Init();    
    
    backgroundProcessing(500);
    yield();
    
    Serial.printf("Running loop ...\n");
 }

void loop(void)
{   // main Loop function
    g_Phoenix.loop();
    webSocket.loop();
    server.handleClient();
    yield();
}

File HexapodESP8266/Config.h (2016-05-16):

//====================================================================
//Project Lynxmotion
//Description: 
// Phoenix hardware configuration file for the Hex Robot.
//
// Date: March 18, 2012
// Programmer: Kurt (aka KurtE)
//
//==================================================================================================================================
#ifndef _CONFIG_h_
#define _CONFIG_h_

// Something's fishy with the max,min,abs stuff in Arduino 8266 Libs
#undef min
#undef max
#undef abs

#define min(a,b) (((a)<(b))?(a):(b))
#define max(a,b) (((a)>(b))?(a):(b))
#define abs(a) ((a < 0 )?(-a):(a))

#define NUM_GAITS    5

//=============================================================================
//[CONSTANTS]
#define BUTTON_DOWN 0
#define BUTTON_UP   1

#define SOUND_PIN   99 //unknown

#define c1DEC   10
#define c2DEC   100
#define c4DEC   10000
#define c6DEC   1000000

#define cRR     0
#define cRM     1
#define cRF     2
#define cLR     3
#define cLM     4
#define cLF     5


//--------------------------------------------------------------------
//[MIN/MAX ANGLES]
#define cRRCoxaMin1     -650      //Mechanical limits of the Right Rear Leg
#define cRRCoxaMax1     650
#define cRRFemurMin1    -900 //  -1050
#define cRRFemurMax1     900 //   750
#define cRRTibiaMin1    -900  // -530
#define cRRTibiaMax1    900

#define cRMCoxaMin1     -650      //Mechanical limits of the Right Middle Leg
#define cRMCoxaMax1     650
#define cRMFemurMin1    -900
#define cRMFemurMax1    900
#define cRMTibiaMin1    -900
#define cRMTibiaMax1    900

#define cRFCoxaMin1     -650      //Mechanical limits of the Right Front Leg
#define cRFCoxaMax1     650
#define cRFFemurMin1    -900
#define cRFFemurMax1    900
#define cRFTibiaMin1    -900
#define cRFTibiaMax1    900

#define cLRCoxaMin1     -650      //Mechanical limits of the Left Rear Leg
#define cLRCoxaMax1     650
#define cLRFemurMin1    -900
#define cLRFemurMax1    900
#define cLRTibiaMin1    -900
#define cLRTibiaMax1    900

#define cLMCoxaMin1     -650      //Mechanical limits of the Left Middle Leg
#define cLMCoxaMax1     650
#define cLMFemurMin1    -900
#define cLMFemurMax1    900
#define cLMTibiaMin1    -900
#define cLMTibiaMax1    900

#define cLFCoxaMin1     -650      //Mechanical limits of the Left Front Leg
#define cLFCoxaMax1     650
#define cLFFemurMin1    -900
#define cLFFemurMax1    900
#define cLFTibiaMin1    -900
#define cLFTibiaMax1    900

//--------------------------------------------------------------------
//[LEG DIMENSIONS]
//Universal dimensions for each leg in mm
#define cXXCoxaLength     45    // 29
#define cXXFemurLength    38    // 57  => 38
#define cXXTibiaLength    90    // 141 => 65-70 WAS 90


#define cRRCoxaLength     cXXCoxaLength	    //Right Rear leg
#define cRRFemurLength    cXXFemurLength
#define cRRTibiaLength    cXXTibiaLength

#define cRMCoxaLength     cXXCoxaLength	    //Right middle leg
#define cRMFemurLength    cXXFemurLength
#define cRMTibiaLength    cXXTibiaLength

#define cRFCoxaLength     cXXCoxaLength	    //Rigth front leg
#define cRFFemurLength    cXXFemurLength
#define cRFTibiaLength    cXXTibiaLength

#define cLRCoxaLength     cXXCoxaLength	    //Left Rear leg
#define cLRFemurLength    cXXFemurLength
#define cLRTibiaLength    cXXTibiaLength

#define cLMCoxaLength     cXXCoxaLength	    //Left middle leg
#define cLMFemurLength    cXXFemurLength
#define cLMTibiaLength    cXXTibiaLength

#define cLFCoxaLength     cXXCoxaLength	    //Left front leg
#define cLFFemurLength    cXXFemurLength
#define cLFTibiaLength    cXXTibiaLength


//--------------------------------------------------------------------
//[BODY DIMENSIONS]
#define cRRCoxaAngle1   -600   //Default Coxa setup angle, decimals = 1
#define cRMCoxaAngle1    0     //Default Coxa setup angle, decimals = 1
#define cRFCoxaAngle1    600   //Default Coxa setup angle, decimals = 1
#define cLRCoxaAngle1    -600  //Default Coxa setup angle, decimals = 1
#define cLMCoxaAngle1    0     //Default Coxa setup angle, decimals = 1
#define cLFCoxaAngle1    600   //Default Coxa setup angle, decimals = 1

#define cRROffsetX      -32    //Distance X from center of the body to the Right Rear coxa
#define cRROffsetZ      54     //Distance Z from center of the body to the Right Rear coxa
#define cRMOffsetX      -68    //Distance X from center of the body to the Right Middle coxa
#define cRMOffsetZ      0      //Distance Z from center of the body to the Right Middle coxa
#define cRFOffsetX      -32    //Distance X from center of the body to the Right Front coxa
#define cRFOffsetZ      -54    //Distance Z from center of the body to the Right Front coxa
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

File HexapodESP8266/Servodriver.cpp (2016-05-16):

/*************************************************** 
  This is a library for our Adafruit 16-channel PWM & Servo driver

  Pick one up today in the adafruit shop!
  ------> http://www.adafruit.com/products/815

  These displays use I2C to communicate, 2 pins are required to  
  interface. For Arduino UNOs, thats SCL -> Analog 5, SDA -> Analog 4

  Adafruit invests time and resources providing this open source code, 
  please support Adafruit and open-source hardware by purchasing 
  products from Adafruit!

  Written by Limor Fried/Ladyada for Adafruit Industries.  
  BSD license, all text above must be included in any redistribution
 ****************************************************/

#include <Wire.h>
#include "Servodriver.h"

// Set to true to print some debug messages, or false to disable them.
#define ENABLE_DEBUG_OUTPUT false


Servodriver::Servodriver(uint8_t addr) {
  _i2caddr = addr;
}

void Servodriver::begin() {
 reset();
}


void Servodriver::reset(void) {
 write8(PCA9685_MODE1, 0x0);
}

void Servodriver::setPWMFreq(float freq) {
  //Serial.print("Attempting to set freq ");
  //Serial.println(freq);
  freq *= 0.9;  // Correct for overshoot in the frequency setting (see issue #11).
  float prescaleval = 25000000;
  prescaleval /= 4096;
  prescaleval /= freq;
  prescaleval -= 1;
  if (ENABLE_DEBUG_OUTPUT) {
    //Serial.print("Estimated pre-scale: "); Serial.println(prescaleval);
  }
  uint8_t prescale = floor(prescaleval + 0.5);
  if (ENABLE_DEBUG_OUTPUT) {
    //Serial.print("Final pre-scale: "); Serial.println(prescale);
  }
  
  uint8_t oldmode = read8(PCA9685_MODE1);
  uint8_t newmode = (oldmode&0x7F) | 0x10; // sleep
  write8(PCA9685_MODE1, newmode); // go to sleep
  write8(PCA9685_PRESCALE, prescale); // set the prescaler
  write8(PCA9685_MODE1, oldmode);
  delay(5);
  write8(PCA9685_MODE1, oldmode | 0xa1);  //  This sets the MODE1 register to turn on auto increment.
                                          // This is why the beginTransmission below was not working.
  //  Serial.print("Mode now 0x"); Serial.println(read8(PCA9685_MODE1), HEX);
}

void Servodriver::setPWM(uint8_t num, uint16_t on, uint16_t off) {
  //Serial.print("Setting PWM "); Serial.print(num); Serial.print(": "); Serial.print(on); Serial.print("->"); Serial.println(off);

  //This code didn't seem to work with chained i2c servo boards
  //Wire.beginTransmission(_i2caddr); 
  //Wire.write(LED0_ON_L+4*num);
  //Wire.write(on);
  //Wire.write(on>>8);
  //Wire.write(off);
  //Wire.write(off>>8);
  //Wire.endTransmission();

  write8((byte)(LED0_ON_L + 4 * num), (byte)on);
  write8((byte)(LED0_ON_H + 4 * num), (byte)(on >> 8));
  write8((byte)(LED0_OFF_L + 4 * num), (byte)off);
  write8((byte)(LED0_OFF_H + 4 * num), (byte)(off >> 8));
}

// Sets pin without having to deal with on/off tick placement and properly handles
// a zero value as completely off.  Optional invert parameter supports inverting
// the pulse for sinking to ground.  Val should be a value from 0 to 4095 inclusive.
void Servodriver::setPin(uint8_t num, uint16_t val, bool invert)
{
  // Clamp value between 0 and 4095 inclusive.
  val = min(val, 4095);
  if (invert) {
    if (val == 0) {
      // Special value for signal fully on.
      setPWM(num, 4096, 0);
    }
    else if (val == 4095) {
      // Special value for signal fully off.
      setPWM(num, 0, 4096);
    }
    else {
      setPWM(num, 0, 4095-val);
    }
  }
  else {
    if (val == 4095) {
      // Special value for signal fully on.
      setPWM(num, 4096, 0);
    }
    else if (val == 0) {
      // Special value for signal fully off.
      setPWM(num, 0, 4096);
    }
    else {
      setPWM(num, 0, val);
    }
  }
}

uint8_t Servodriver::read8(uint8_t addr) {
  Wire.beginTransmission(_i2caddr);
  Wire.write(addr);
  Wire.endTransmission();

  Wire.requestFrom((uint8_t)_i2caddr, (uint8_t)1);
  return Wire.read();
}

void Servodriver::write8(uint8_t addr, uint8_t d) {
  Wire.beginTransmission(_i2caddr);
  Wire.write(addr);
  Wire.write(d);
  Wire.endTransmission();
}

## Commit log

2016-05-16 Initial Version
    [bottom.stl, coxa_l.stl, coxa_r.stl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]
2016-05-16 smaller switch hole, smaller stand offs
    [bottom.stl, hexajpod.scad]
2016-05-18 Updated the bill of materials
2016-05-18 Updated BOM
2016-05-18 aligned dc-dc converter holes
    [bottom.stl, hexajpod.scad]
2018-01-31 Some changes
    [hexajpod_t.scad, hexajpodbottom.dxf]
